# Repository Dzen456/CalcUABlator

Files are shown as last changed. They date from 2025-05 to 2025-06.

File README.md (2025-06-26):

<a href=https://github.com/Dzen456/CalcUABlator>

</a>

<p style="text-align:center;">
A robot capable of doing mathematical operations using Computer Vision.

This document contains instructions of the robot's functionality and usage, and the requirements necessary for this code and hardware to work.
</p>

## Table of contents:

- [Description](#Description)
- [Directories](#Directories)
- [Demo](#Demo)
- [Installation](#Installation)
  - [Hardware](#Hardware)
      - [Fritzing](#Fritzing)
  - [Software](#Software)
      - [Specs](#Specs)
      - [Requirements](#Requirements)
- [Simulation](#Simulation)
- [How to Use](#How_to_Use)
- [Contributions](#Contributions)
- [License](#License)
- [Authors](#Authors)
- [Bibliography](#Bibliography)

## Description:
In this project, we wanted to create a robot capable of solving mathematical operations using Computer Vision and some of the things we learned during this subject. 

On the one hand, when considering this idea, you may think of applications or websites like PhotoMath or Symbolab, so you can think that this robot the same as these apps, but in a more tangible way.

On the other hand, all the pieces used for this robot are recycled: the main structure of the robot is a scara made in 2017, and the camera and Raspberry Pi structure were made from a wooden plank from an old pallet.

Finally, we developed the software to detect an operation, solve it, and write the solution on real paper. We also created a CoppeliaSim scene and a Jupyter Notebook so you can simulate the entire robot process in a simple and visual way.

See <a href=https://github.com/Dzen456/CalcUABlator/blob/main/CREATIVE%20PROCESS.md> CREATIVE PROCESS </a> to read more about the making of this project.

## Directories:

CalcUABlator has the following directories:

- CoppeliaSim_CalcUABlator: This folder contains the CoppeliaSim scene and the Jupyter Notebook of the robot, where you can simulate his behaviour and usage.
```cmd
CoppeliaSim_CalcUABlator/
├── test_texture/
│   └── test_texture.jpg
├── CoppeliaSim.gif
├── CoppeliaSim_CalcUABlator.ttt
├── CoppeliaSim_CalcUABlator_script.ipynb
├── remoteApi.dll
├── sim.py
└── simConst.py
```
- Hardware_CalcUABlator: This folder contains the components, budget and blueprints for the fritzing of the robot, required for his correct construction. The diagram must be followed; otherwise, the robot likely won't work.
```cmd
Hardware_CalcUABlator/
├── Fritzing_CalcUABlator/
│   ├── MSStepperDriverTable.PNG
│   ├── calcUABlator-fritzing.fzz
│   ├── calcUABlator-fritzing_bb.png
│   └── references.txt
├── budget.pdf
├── budget.xlsx
├── components.pdf
└── components.xlsx
```
- Old version - 3D Model and ideas: This folder contains an old, unused version of the robot for researching purposes, with the dimensions, list of components, and a code for the camera.
```cmd
Old version - 3D Model and ideas/
├── OLD_calcUABlator/
│   ├── Pen Holder/
│   │   ├── Comment.txt
│   │   ├── RLP_PenHolder.blend
│   │   ├── part1.png
│   │   ├── part2.png
│   │   ├── part3.png
│   │   └── part4.png
│   ├── background_test/
│   │   └── christmas_photo_studio_07_4k.exr
│   ├── List of components (No Hardware) - 22-04-2025.pdf
│   └── RLP_Robot_sketch2.blend
├── Measurement_Confirmation_Script.py
├── Raspberry_Structure_Measurements.txt
└── Raspberry_Structure_Measurements_Trigonometry (Comments in Spanish).pdf
```
- Software_CalcUABlator: This folder contains the function diagram of the robot, with all the variables and functions that the robot manages in the Raspberry Pi and Arduino modules, all the RaspberryPi and Arduino scripts and a requirements.txt for the installation.
```cmd
Software_CalcUABlator/
├── Arduino/
│   ├── OnlyServo/
│   │   └── sketch_may14a.ino
│   ├── Servo+Steppers/
│   │   └── sketch_may27a.ino
│   └── Main/
│       └── Main.ino
├── RaspberryPi
│   ├── capture_image.py
│   ├── connect_arduino.py
│   ├── main.py
│   ├── move_robot.py
│   └── text_recognition.py
├── SoftwareSchema.pdf
├── requirements.txt
└── specs.txt
```

## Demo:
Click <a href=https://youtu.be/mdDsb5YC6hA> here </a> to see the demo video.
<a href=https://youtu.be/mdDsb5YC6hA>
  


</a>

## Installation:

### Hardware

Making this robot requieres all of the following **hardware components**, or at least similar to:

| <a href=https://tienda.bricogeek.com/arduino-original/1845-arduino-uno-r4-wifi.html> Arduino UNO 4 WiFi </a> | <a href=https://tienda.bricogeek.com/placas-raspberry-pi/1330-raspberry-pi-4-model-b-4-gb.html > Raspberry Pi 4 </a> |
| :---: | :---: |
|  |  |
| <a href=https://tienda.bricogeek.com/accesorios-raspberry-pi/822-camara-raspberry-pi-v2-8-megapixels.html> **Raspberry Pi v2 Cam** </a> | <a href=https://tienda.bricogeek.com/fuentes-de-alimentacion/775-fuente-de-alimentacion-atx-coolbox-500w.html> **Power Supply ATX 500W** </a> |
|  |  |
| <a href=https://tienda.bricogeek.com/motores-paso-a-paso/1360-motor-nema-17-35kg-con-conector-y-cable.html> **Nema 17 stepper** </a> | <a href=https://tienda.bricogeek.com/controladores-motores/553-pololu-a4988-stepstick-prusa-reprap.html> **Stepper Driver Pololu A4988** </a> |
|  |  |
| <a href=https://tienda.bricogeek.com/motores/118-servomotor-de-rotacion-continua-s3003-360-grados.html> **Servo S3003** </a> |  |
|  |  |

<!-- Source Power Supply for Raspberry Pi 4 - 5V/2.5A -->
- You will need to have a **Power Supply for the Raspberry Pi 4 of 5V/2.5A**.
- You should **use the +12V (Yellow output) from the ATX Power Supply** to power the stepper drivers.

- Maybe you should **calibrate the two stepper drivers to a VRef of 1.2V** (see how to do this in this video: https://youtu.be/wcLeXXATCR4?t=462).


#### Fritzing:
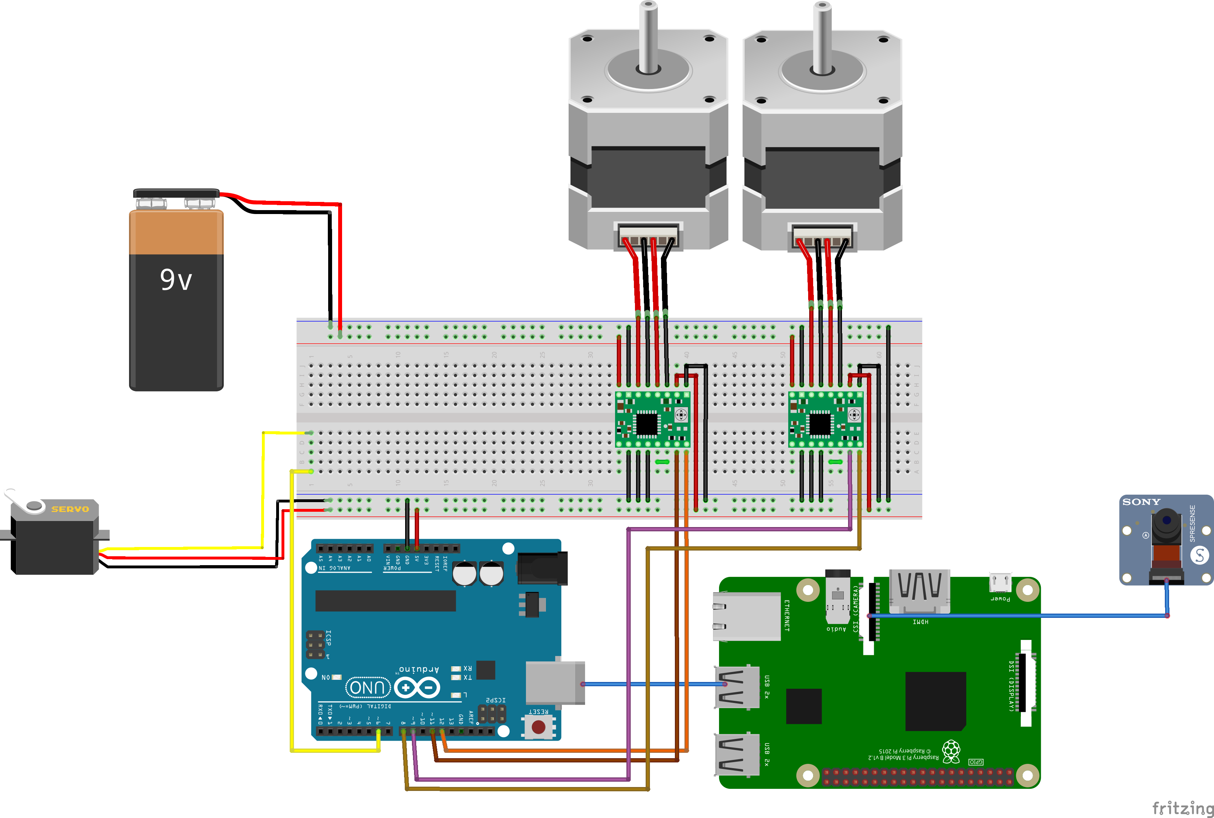
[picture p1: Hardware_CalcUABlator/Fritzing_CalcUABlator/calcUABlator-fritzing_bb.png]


Also, it is required to have the following **additional pieces**:

- Arms Support: (estimated parameters: length - 18 cm / width - 5 cm / thickness - 0.25 cm)
- Big Metal Axis: (estimated parameters: diameter - 2 cm / height - 12 cm)
- Big Axis Wheel: (estimated parameters: wheel diameter - 3 cm / hole wheel diameter - 2 cm)
- Small Metal Axis: (estimated parameters: diameter - 2 cm / height - 5 cm)
- Smal Wheel Axis: (estimated parameters: wheel diameter - 3 cm / hole wheel diameter - 2 cm)
- Screws: 20 screws of 1 cm, 4 screws of 3 cm
- Pen Support Piece: (estimated parameters: length - 5 cm / width - 1 cm / square zone hole - 1x1 cm)
- Wood Platform: (estimated parameters: length - 42 cm / width - 32 cm / thickness - 1 cm)
- Raspberry Structure Support: (estimated parameters: length - 8 cm / width - 8 cm / height - 30 cm)
- Raspberry Structure Superior Support: (estimated parameters: length - 30 cm / width - 8 cm / thickness - 2 cm)
- 2-4 brackets
- Rubber Strap
- Also some extra pieces between the arms and the axis supports.

### Software



#### Specs:

IDEs:
- Python (Pycharm, VS Code, Spyder,...)
- Jupyter Notebook 7+ (Downloaded from the website or Anaconda)
- Arduino IDE (Web or desktop version)

Other software:
- Coppelia 4.7
- Blender 4.1
- Python 3.11

#### Requirements:
```shell
numpy
opencv-python
matplotlib
easyocr
sympy
pyserial
```

If you just want to run the simulation, see [Simulation](#Simulation). 

If you want to make it work in the real life, see [How to Use](#How-to-Use).

## Simulation:

1. Clone this repo.
 ```bash
 git clone https://github.com/Dzen456/CalcUABlator.git
 ```
   
2. You have to open and run the CoppeliaSim_CalcUABlator.ttt file on the CoppeliaSim
3. Then, execute the CoppeliaSim_CalcUABlator_script.ipynb notebook to activate the demo of the robot. It is possible to change the test texture in the folder test_texture to test the robot capacities.
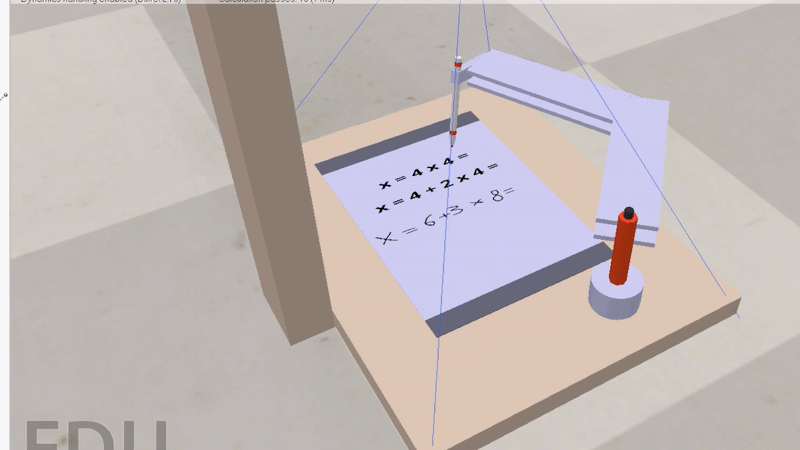
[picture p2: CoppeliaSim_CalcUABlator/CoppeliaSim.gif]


## How to Use:

1. Clone this repo.
 ```bash
 git clone https://github.com/Dzen456/CalcUABlator.git
 ```

2. Install the required libraries.
Using pip:
```bash
pip install requirements.txt
```
Using conda:
```bash
conda install -c requirements.txt
```

3. Execute python script in each directory.

4. To run the robot's Arduino UNO 4 WiFi, you'll have to connect the device to the arduino with a USB cable to be able to run the code correctly. You'll also need to build the robot using the components described [above](#Hardware) and the blueprints for the [circuits](#Fritzing) and structure.

5. Add star to this repo if you like it!

## Contributions:

See <a href=https://github.com/Dzen456/CalcUABlator/blob/main/CONTRIBUTING.md> CONTRIBUTING </a> if you want to contribute to this project.

## License:

This project has a <a href=https://github.com/Dzen456/CalcUABlator/blob/main/LICENSE> Creative Commons License </a>.

## Authors:

- Yanhao Lin
- Isaac Sánchez Amat
- Jofre Segura Montagut
- Raúl Velázquez Gómez
- David Zheng

## Bibliography:

- Arduino UNO R4 Wifi: https://tienda.bricogeek.com/arduino-original/1845-arduino-uno-r4-wifi.html 
- Raspberry Pi 4: https://tienda.bricogeek.com/placas-raspberry-pi/1330-raspberry-pi-4-model-b-4-gb.html 
- Nema 17 stepper: https://tienda.bricogeek.com/motores-paso-a-paso/1360-motor-nema-17-35kg-con-conector-y-cable.html 
- Power Supply ATX 500W: https://tienda.bricogeek.com/fuentes-de-alimentacion/775-fuente-de-alimentacion-atx-coolbox-500w.html 
- Stepper Driver Pololu A4988: https://tienda.bricogeek.com/controladores-motores/553-pololu-a4988-stepstick-prusa-reprap.html 
- Raspberry Pi v2 Cam: https://tienda.bricogeek.com/accesorios-raspberry-pi/822-camara-raspberry-pi-v2-8-megapixels.html 
- Servo S3003: https://tienda.bricogeek.com/motores/118-servomotor-de-rotacion-continua-s3003-360-grados.html

- Getting started with arduino: https://docs.arduino.cc/tutorials/uno-rev3/getting-started/ 
- Connect Raspberry Pi to Arduino: https://www.youtube.com/watch?v=xc9rUI0F6Iw 
- Connect stepper and stepper driver to Arduino (1): https://www.youtube.com/shorts/hTjXpgDDzUI 
- Connect stepper and stepper driver to Arduino (2): 
https://www.youtube.com/watch?v=nLV0fjUWI-g 
- Connect servo motor to Arduino: https://www.youtube.com/watch?v=rM1Zk05Xdlk 
- Connect Raspberry cam to Raspberry Pi: https://www.youtube.com/watch?v=VzYGDq0D1mw 
- Control stepper motor with Arduino: https://docs.arduino.cc/learn/electronics/stepper-motors/ 
- Control servo motor: https://docs.arduino.cc/learn/electronics/servo-motors/ 
- Connect, calibrate and control NEMA 17 steppers with arduino: https://www.youtube.com/watch?v=wcLeXXATCR4 
- Raspberry Pi v2 Cam angles: https://raspberrypi-guide.github.io/electronics/camera-positioning

- Robot from 2017: https://rlpengineeringschooluab2017.wordpress.com/2017/05/30/turing-drawing/
- Robótica, Llenguatge i Programació class notes.

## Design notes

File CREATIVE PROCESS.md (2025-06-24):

# Creative Process

This document explains the creative process of the project.

At first, we discussed a lot of posible ideas for a robot. After long deliberations, we came at the conclusion that it would be interesting to make a robot that would be capable of doing mathematical operations.

This robot may feel useless because there are already other resources that are capable of doing something similar without making a full-sized robot, for example, aplications like PhotoMath or webs like Symbolab, but we thought that it could have some interesting applications at some environments like a school, because it would be easier to teach math using this robot in a more autonomous way, than just writing an operation and making it manually. This, however, required to make a robot capable of doing the process of the operation too, which was inviable due to our time and resources, so we decided to make this robot as a kind of research that could be used at the future for other projects too. Also, these types of online services usually require cookies or other data-collecting methods that would be avoided if a robot is used instead, so it wasn't a bad idea to make something for that purpose.

Our first step was to decide the robot components without surpassing the budget, but we had to order too many things and we had to surpass the budget a bit, but nothing serious. We then started to model the robot: we had to do the base and decide the 3D pieces and the shape of the robot. This was more complex than it sounds, but then we got permission to use another robot as a base for our project, which was very useful and solved a lot of things.

We then started to make the simulation of the robot and we worked on the camera support for the robot as an additional piece. The simulation was made sucessfully and we got wood material from the OpenLabs of our department, material that we modified on these same instalations to obtain the support piece for the camera. We also made the fritzing to knew how the circuits of the robot would be conected for them to work and we also did the functions diagram to have an idea of what would be the programming structure of the robot.

Once we obtained the hardware that we requested, we finally were able to put all of the things together, and make the robot work. But it turned out to not be that easy, because the fritzing didn't work at first. After a long series of trials and errors, we concluded that the problem was one driver that didn't allow the other engine to work fine because we couldn't callibrate it correctly due to his own set limit. We also had to change the principal band because it hadn't enought tension to be able to make the robot work, which was a problem too, and we had to change the drivers a lot of times due to the set limit that didn't allow us to give enough strength to the robot (we knew that the problem was the second driver because we got a driver that worked but we only had one to make all of the robot work). Finally, we could make the robot work after trying a lot of drivers, and we took it home to make the video for the presentation.

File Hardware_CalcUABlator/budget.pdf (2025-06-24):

Name | Price | Units | Total | URL
Arduino UNO Rev. 3 | (€ | 28,98) | 1,00 | (€ | 28,98) https://tienda.bricogeek.com/arduino/305-arduino-uno-r3.html
Raspberry Pi 3 B+ | (€ | 49,97) | 1,00 | (€ | 49,97) https://tienda.bricogeek.com/placas-raspberry-pi/1089-raspberry-pi-3-b-plus.html
Fuente Alimentación Raspberry Pi 3 - 5V/2.5A | (€ | 9,56) | 1,00 | (€ | 9,56) https://tienda.bricogeek.com/accesorios-raspberry-pi/813-alimentador-raspberry-pi-3-5v25a.html
Cámara Raspberry Pi v2 - 8 Megapixels | (€ | 24,14) | 1,00 | (€ | 24,14) https://tienda.bricogeek.com/accesorios-raspberry-pi/822-camara-raspberry-pi-v2-8-megapixels.html
Motor NEMA 17 / 3.5Kg con conector y cable | (€ | 11,13) | 2,00 | (€ | 22,26) https://tienda.bricogeek.com/motores-paso-a-paso/1360-motor-nema-17-35kg-con-conector-y-cable.html
Controlador de motores paso a paso 3.5A (TB6600) | (€ | 24,14) | 2,00 | (€ | 48,28) https://tienda.bricogeek.com/controladores-motores/992-controlador-de-motores-paso-a-paso-35a-tb6600.html
Servo estándar S3003, 360 Grados | (€ | 6,66) | 1,00 | (€ | 6,66) https://tienda.bricogeek.com/motores/118-servomotor-de-rotacion-continua-s3003-360-grados.html
(Piezas de soporte para los controladores?)
Fuente de alimentación ATX COOLBOX 500W | 19,97 | 1 | 19,97 https://tienda.bricogeek.com/fuentes-de-alimentacion/775-fuente-de-alimentacion-atx-coolbox-500w.html
TOTAL | (€ 209,82)
*Suposem que es pot alimentar l'arduino amb la ATX*
(Si no, faria falta una alimentació per l'arduino)

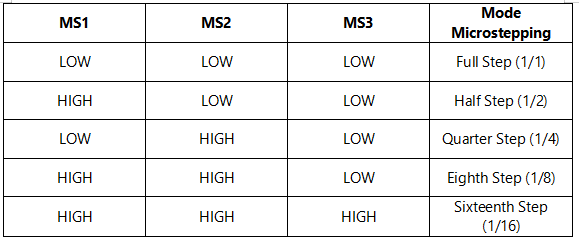
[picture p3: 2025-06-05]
Hardware_CalcUABlator/Fritzing_CalcUABlator/MSStepperDriverTable.PNG

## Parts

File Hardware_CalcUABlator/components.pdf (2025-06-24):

| Largo (mm) | Ancho (mm) | Alto (mm) | Peso (g) | Plano medidas | Plano conexiones | Datos/contenido adcional
Arduino UNO R3 | 68.6 | 53.2 | 12.5 | 25 | Ver Medidas (https://kicad-info.s3.dualstack.us-west-2.amazonaws.com/original/2X/e/ed545e8aaf2ff57f95a87286ba8bb29ea2749de6.jpeg) | Ver circuito (https://www.jameco.com/Jameco/workshop/CircuitNotes/arduino-uno-pinout.png)
Raspberry Pi 3 B+ (https://tienda.bricogeek.com/placas-raspberry-pi/1089-raspberry-pi-3-b-plus.html) | 85.0 | 56.0 | 17.0 | 60 | Ver Medidas (https://raspiworld.com/images/other/drawings/Raspberry-Pi-1-2-3-Model-B.jpg) | Ver circuito (https://www.jameco.com/Jameco/workshop/CircuitNotes/raspberry_pi_circuit_note_fig2.jpg) | Vídeo de como connectar raspberry a arduino (https://www.youtube.com/watch?v=xc9rUI0F6Iw)
Fuente Alimentación Raspberry Pi 3 - 5V/2.5A (https://tienda.bricogeek.com/accesorios-raspberry-pi/813-alimentador-raspberry-pi-3-5v25a.html) | 73.2 | 45.1 | 35.1 | 150
Cámara Raspberry Pi v2 - 8 Megapixels (https://tienda.bricogeek.com/accesorios-raspberry-pi/822-camara-raspberry-pi-v2-8-megapixels.html) | 25.0 | 24.0 | 9.0 | 3 | Ver Medidas (https://www.raspberrypi-spy.co.uk/wp-content/uploads/2013/05/Raspberry-Pi-Camera-Module-Diagram.png) | Ver circuito (https://docs.arducam.com/Raspberry-Pi-Camera/Low-Light/picture/arducam_wiki_rpi_imx708_hardware_picture_1.png) | Campo de visión horizontal (CdV): 62,2 grados. Campo de visión vertical (CdV): 48,8 grados, Vídeo de como connectar la camara raspberry pi
Motor NEMA 17 / 3.5Kg con conector y cable x2 (https://tienda.bricogeek.com/motores-paso-a-paso/1360-motor-nema-17-35kg-con-conector-y-cable.html) | 42.0 | 42.0 | 40.0 | 270 | Ver Medidas (https://tienda.bricogeek.com/1820-thickbox_default/motor-paso-a-paso-nema-17-32kg-cm.jpg) | Ver circuito (https://protosupplies.com/wp-content/uploads/2018/04/DRV8825-Driver-Minimal-Setup.jpg) | Vídeo de como conectar controlador de motores y steppers con arduino , Otro vídeo
Controlador de motores paso a paso 3.5A (TB6600) x2 (https://tienda.bricogeek.com/controladores-motores/992-controlador-de-motores-paso-a-paso-35a-tb6600.html) | 96.0 | 56.0 | 33.0 | 200 | Ver Medidas (https://comtongkorea.cafe24.com/web/image/2218_KC0001024/640602054294/D640602054294_9.jpg) | Ver circuito (https://tienda.bricogeek.com/4135-large_default/controlador-de-motores-paso-a-paso-35a-tb6600.jpg) | Vídeo de como conectar controlador de motores y steppers con arduino (https://www.youtube.com/shorts/hTjXpgDDzUI)
Servo estándar S3003, 360 Grados (https://tienda.bricogeek.com/motores/118-servomotor-de-rotacion-continua-s3003-360-grados.html) | 39.5 | 20.0 | 35.6 | 53 | Ver Medidas (https://tienda.bricogeek.com/9440-thickbox_default/servo-6-kg-300-grados-con-proteccion.jpg) | Ver circuito (https://cdn.shopify.com/s/files/1/0587/2130/4757/files/KG085.jpg?v=1638961040) | Vídeo de como conectar servo motor al arduino (https://www.youtube.com/watch?v=rM1Zk05Xdlk)
Fuente de alimentación ATX COOLBOX 500W (https://tienda.bricogeek.com/fuentes-de-alimentacion/775-fuente-de-alimentacion-atx-coolbox-500w.html) | 140.0 | 150.0 | 85.0 | 2180

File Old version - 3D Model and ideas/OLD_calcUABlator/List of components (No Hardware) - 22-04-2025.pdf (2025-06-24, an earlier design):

Arm supports: To be determined.
- Estimate:
- Length: 18 cm
- Width: 5 cm
- Thickness: 0.25 cm

Intermediate pieces between arms and axle supports: To be determined.

Large axle (Metal):
- Diameter: 2 cm
- Height: About 12 cm

Large axle wheel (3D printed):
- Wheel diameter: 3 cm
- Hole diameter: 2 cm (goes to the large axle)

Small axle (Metal):
- Diameter: 2 cm
- Height: About 5 cm

Small axle wheel (3D printed):
- Wheel diameter: 3 cm
- Hole diameter: 2 cm (goes to the small axle)

Screws (Estimate):
- About 20 units,1 cm long
- About 4 bigger, about 3 cm long (Those that go into the wood, in the Raspberry structure, above)

Pen holder piece (3D printed):
- Length: 5 cm
- Width: 1 cm
- Square hole area, approximately 1x1 cm

Wooden platform:
- Length: 42 cm
- Width: 32 cm
- Thickness: 1 cm

DC bracket, Arm 1, to be determined

Raspberry structure:
- Base support (still to be determined with camera angles, wood):
- Length: 8 cm
- Width: 8 cm
- Height: 30 cm
- Upper support (where the camera goes, wood):
- Length: 30 cm
- Width: 8 cm
- Thickness: 2 cm

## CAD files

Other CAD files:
Old version - 3D Model and ideas/OLD_calcUABlator/Pen Holder/RLP_PenHolder.blend
Old version - 3D Model and ideas/OLD_calcUABlator/RLP_Robot_sketch2.blend

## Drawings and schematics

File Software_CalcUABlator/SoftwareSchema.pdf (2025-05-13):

# SOFTWARE SCHEMA

# Raspberry Pi

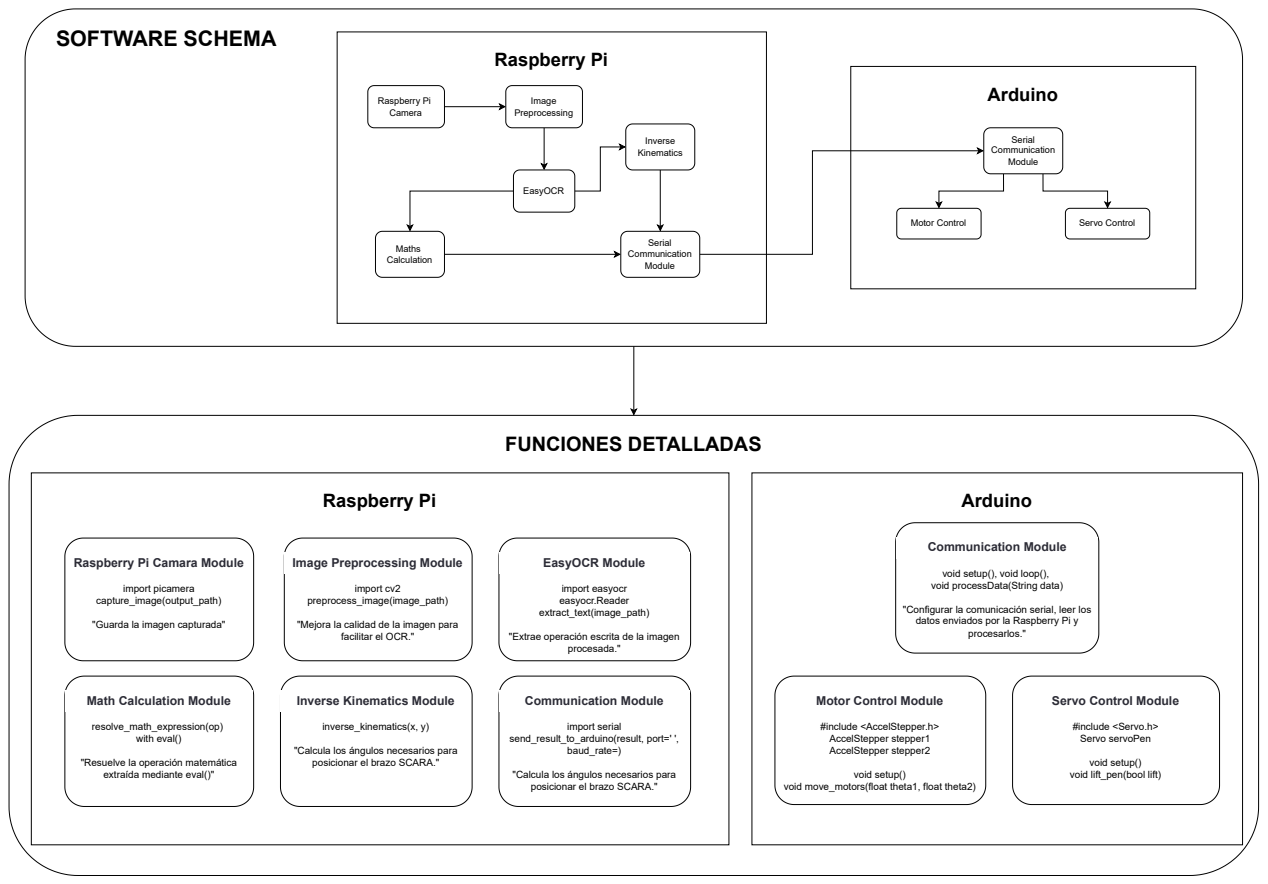
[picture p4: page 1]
Raspberry Pi; Arduino; Camera; Image Preprocessing; EasyOCR; Maths Calculation; Inverse Kinematics; Serial Communication Module; Motor Control; Servo Control; import picamera capture_image(output_path); import cv2 preprocess_image(image_path); EasyOCR Module; import easyocr easyocr.Reader extract_text(image_path); procesada."; resolve_math_expression(op) with eval(); inverse_kinematics(x, y); Communication Module; import serial send_result_to_arduino(result, port=' ', baud_rate=)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

Raspberry Pi Camara Module

Image Preprocessing Module

void setup(), void loop(),
void processData(String data)

"Configurar la comunicación serial, leer los
datos enviados por la Raspberry Pi y

"Guarda la imagen capturada"

"Mejora la calidad de la imagen para

facilitar el OCR."

"Extrae operación escrita de la imagen

Math Calculation Module

Inverse Kinematics Module

Motor Control Module

Servo Control Module

"Calcula los ángulos necesarios para
posicionar el brazo SCARA."

"Resuelve la operación matemática
extraída mediante eval()"

void setup()
void lift_pen(bool lift)

void move_motors(float theta1, float theta2)

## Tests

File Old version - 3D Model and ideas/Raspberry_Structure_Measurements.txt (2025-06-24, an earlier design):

Ideal Woods:

Regarding height:
One 40.5 cm, which will be the support, and then the top piece, which will be 2 cm high.

Base square:
8x8? cm

Top piece rectangle:
8? x 20+8? -> Depends on the previous piece.

Final Measurements (If possible):

Base piece:

Height: 40.5 cm
Width: 8 cm
Length: 8 cm

Top piece (where the camera will go):

Height: 2 cm
Width: 8 cm
Length: 28 cm

We'll see what we can get at the Open Labs.

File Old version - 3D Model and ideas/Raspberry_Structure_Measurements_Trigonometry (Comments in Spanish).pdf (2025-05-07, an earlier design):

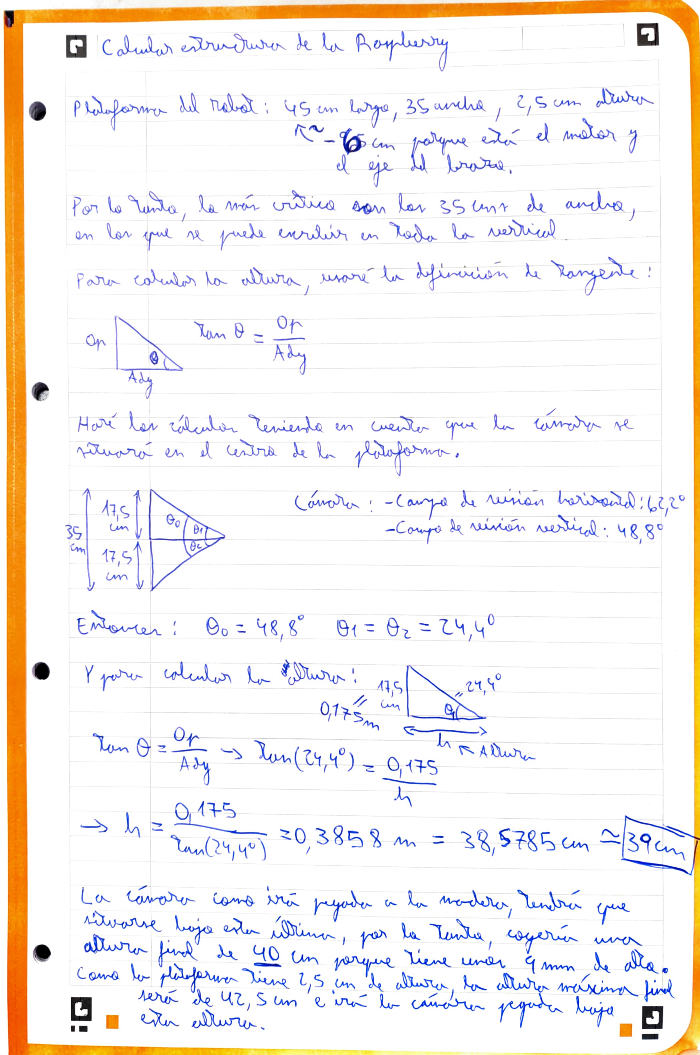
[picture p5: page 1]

Eeen

Bo

Aby
75

tgo,3swndha

0175m
Lon(r,) 915

z0 38 m = 38,5785 Cn 39

wn

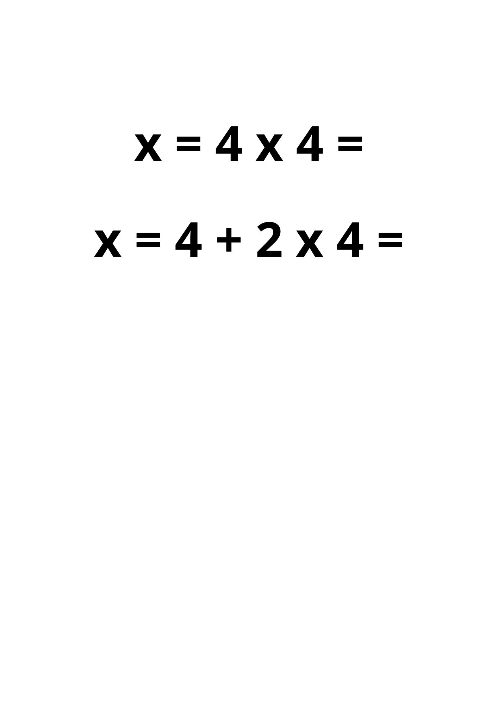
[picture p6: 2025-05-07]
CoppeliaSim_CalcUABlator/test_texture/test_texture.jpg

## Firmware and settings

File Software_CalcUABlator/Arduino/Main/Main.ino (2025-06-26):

#include <AccelStepper.h>
#include <Servo.h>

// Configuración del pin del servomotor
#define SERVO_PIN 6

// Crear un objeto Servo
Servo penServo;

// Configuración de los pines para los motores
#define MOTOR1_PIN_STEP 11
#define MOTOR1_PIN_DIR 12
#define MOTOR2_PIN_STEP 9
#define MOTOR2_PIN_DIR 8

const int width = 50, height = 50; // Ancho y alto del dígito

// Ángulo de rotación (en grados)
const float rotation_angle_degrees = -20.0; // Ajusta este valor según sea necesario
const float rotation_angle_radians = rotation_angle_degrees * PI / 180.0;

// Crear objetos AccelStepper para cada motor
AccelStepper stepper1(AccelStepper::DRIVER, MOTOR1_PIN_STEP, MOTOR1_PIN_DIR);
AccelStepper stepper2(AccelStepper::DRIVER, MOTOR2_PIN_STEP, MOTOR2_PIN_DIR);

bool stopRunning = false;
void setup() {
  Serial.begin(9600);  // Inicializar comunicación serial
  
  // Configurar velocidad máxima y aceleración para cada motor
  stepper1.setMaxSpeed(1000);
  stepper1.setAcceleration(500);
  
  stepper2.setMaxSpeed(1000);
  stepper2.setAcceleration(500);

  // Adjuntar el servomotor al pin especificado
  penServo.attach(SERVO_PIN);

  // Posición inicial (bolígrafo levantado)
  lift_pen(true);
}

void move_to_position_rotated(int x, int y, int centerX, int centerY) {
  int* rotatedCoords = rotate_point(x, y, centerX, centerY);
  int rotatedX = rotatedCoords[0];
  int rotatedY = rotatedCoords[1];

  // Mover los motores a las coordenadas rotadas
  stepper1.moveTo(rotatedX);
  stepper2.moveTo(rotatedY);

  while (stepper1.distanceToGo() != 0 || stepper2.distanceToGo() != 0) {
    stepper1.run();
    stepper2.run();
  }
}

int* rotate_point(int x, int y, int centerX, int centerY) {
  // Calcular las coordenadas relativas al centro
  int relativeX = x - centerX;
  int relativeY = y - centerY;

  // Aplicar la fórmula de rotación
  float rotatedX = relativeX * cos(rotation_angle_radians) - relativeY * sin(rotation_angle_radians);
  float rotatedY = relativeX * sin(rotation_angle_radians) + relativeY * cos(rotation_angle_radians);

  // Volver a la posición absoluta
  static int rotatedCoords[2];
  rotatedCoords[0] = round(rotatedX + centerX);
  rotatedCoords[1] = round(rotatedY + centerY);
  return rotatedCoords;
}

void write_number(int number) {
  // Levantar el bolígrafo antes de empezar
  lift_pen(true);

  // Obtener la posición actual del brazo
  int currentX = stepper1.currentPosition();
  int currentY = stepper2.currentPosition();

  // Mover al punto inicial relativo a la posición actual

  // Dibujar el número según el valor recibido
  switch (number) {
    case 0:
      draw_zero(currentX, currentY);
      break;
    case 1:
      draw_one(currentX, currentY);
      break;
    case 2:
      draw_two(currentX, currentY);
      break;
    case 3:
      draw_three(currentX, currentY);
      break;
    case 4:
      draw_four(currentX, currentY);
      break;
    case 5:
      draw_five(currentX, currentY);
      break;
    case 6:
      draw_six(currentX, currentY);
      break;
    case 7:
      draw_seven(currentX, currentY);
      break;
    case 8:
      draw_eight(currentX, currentY);
      break;
    case 9:
      draw_nine(currentX, currentY);
      break;
    default:
      Serial.println("Número no válido.");
      return;
  }

  // Levantar el bolígrafo después de terminar
  lift_pen(true);
}

void loop() {
  if (stopRunning == true) {
    return;
  }
  if (Serial.available() > 0) {
    String receivedData = Serial.readStringUntil('\n');  // Read until newline character
    receivedData.trim();  // Remove any extra whitespace or carriage returns

    // Split the string into three parts using the delimiter (comma)
    int firstCommaIndex = receivedData.indexOf(',');
    int secondCommaIndex = receivedData.indexOf(',', firstCommaIndex + 1);

    if (firstCommaIndex != -1 && secondCommaIndex != -1) {  // Ensure delimiters exist
      String value1Str = receivedData.substring(0, firstCommaIndex);
      String value2Str = receivedData.substring(firstCommaIndex + 1, secondCommaIndex);
      String value3Str = receivedData.substring(secondCommaIndex + 1);

      // Convertir a int
      int value1 = value1Str.toInt();
      int value2 = value2Str.toInt();
      int value3 = value3Str.toInt();

      Serial.print("Received Value 1: ");
      Serial.println(value1);
      Serial.print("Received Value 2: ");
      Serial.println(value2);
      Serial.print("Received Value 3: ");
      Serial.println(value3);
      
      stepper1.moveTo(value1 * (200.0 / 360.0) + 40);  // Convierte grados a pasos
      while (stepper1.distanceToGo() != 0) {
        stepper1.run(); 
      }
      delay(1000);  // Esperar 1 segundo

      stepper2.moveTo(value2 * (200.0 / 360.0) - 100);  // Convierte grados a pasos
      while (stepper2.distanceToGo() != 0) {
        stepper2.run();
      }
      delay(1000);

      write_number(value3);
      stopRunning = true;
      return;
      
    }
  }
  /*
  lift_pen(false);
  delay(1000);
  lift_pen(true);
  delay(1000);
  */
}

void draw_zero(int startX, int startY) {
  lift_pen(false);  // Bajar el bolígrafo
  move_to_position_rotated(startX, startY, startX, startY);                  // Punto inicial
  move_to_position_rotated(startX + width, startY, startX, startY);          // Línea horizontal superior
  move_to_position_rotated(startX + width, startY + height, startX, startY); // Línea vertical derecha
  move_to_position_rotated(startX, startY + height, startX, startY);         // Línea horizontal inferior
  move_to_position_rotated(startX, startY, startX, startY);                  // Línea vertical izquierda
  lift_pen(true);  // Levantar el bolígrafo
}

void draw_one(int startX, int startY) {
  lift_pen(false);  // Bajar el bolígrafo
  move_to_position_rotated(startX + width / 2, startY, startX, startY);       // Punto inicial
  move_to_position_rotated(startX + width / 2, startY + height, startX, startY); // Línea vertical
  lift_pen(true);  // Levantar el bolígrafo
}

void draw_two(int startX, int startY) {
  lift_pen(false);  // Bajar el bolígrafo
  move_to_position_rotated(startX, startY, startX, startY);                   // Punto inicial
  move_to_position_rotated(startX + width, startY, startX, startY);           // Línea horizontal superior
  move_to_position_rotated(startX + width, startY + height / 2, startX, startY); // Línea diagonal derecha
  move_to_position_rotated(startX, startY + height / 2, startX, startY);      // Línea horizontal central
  move_to_position_rotated(startX, startY + height, startX, startY);          // Línea vertical izquierda
  move_to_position_rotated(startX + width, startY + height, startX, startY);  // Línea horizontal inferior
  lift_pen(true);  // Levantar el bolígrafo
}

void draw_three(int startX, int startY) {
  lift_pen(false);  // Bajar el bolígrafo
  move_to_position_rotated(startX, startY, startX, startY);                   // Punto inicial
  move_to_position_rotated(startX + width, startY, startX, startY);           // Línea horizontal superior
  move_to_position_rotated(startX + width, startY + height / 2, startX, startY); // Línea vertical derecha
  move_to_position_rotated(startX, startY + height / 2, startX, startY);      // Línea horizontal central
  move_to_position_rotated(startX + width, startY + height / 2, startX, startY); // Línea vertical derecha
  move_to_position_rotated(startX + width, startY + height, startX, startY);  // Línea horizontal inferior
  lift_pen(true);  // Levantar el bolígrafo
}

void draw_four(int startX, int startY) {
  lift_pen(false);  // Bajar el bolígrafo
  move_to_position_rotated(startX, startY, startX, startY);                   // Punto inicial
  move_to_position_rotated(startX, startY + height / 2, startX, startY);      // Línea vertical izquierda
  move_to_position_rotated(startX + width, startY + height / 2, startX, startY); // Línea horizontal central
  move_to_position_rotated(startX + width, startY, startX, startY);           // Línea vertical derecha
  move_to_position_rotated(startX + width, startY + height, startX, startY);  // Línea vertical derecha
  lift_pen(true);  // Levantar el bolígrafo
}

void draw_five(int startX, int startY) {
  lift_pen(false);  // Bajar el bolígrafo
  move_to_position_rotated(startX + width, startY, startX, startY);           // Punto inicial
  move_to_position_rotated(startX, startY, startX, startY);                   // Línea horizontal superior
  move_to_position_rotated(startX, startY + height / 2, startX, startY);      // Línea vertical izquierda
  move_to_position_rotated(startX + width, startY + height / 2, startX, startY); // Línea horizontal central
  move_to_position_rotated(startX + width, startY + height, startX, startY);  // Línea vertical derecha
  move_to_position_rotated(startX, startY + height, startX, startY);          // Línea horizontal inferior
  lift_pen(true);  // Levantar el bolígrafo
}

void draw_six(int startX, int startY) {
  lift_pen(false);  // Bajar el bolígrafo
  move_to_position_rotated(startX + width, startY, startX, startY);           // Punto inicial
  move_to_position_rotated(startX, startY, startX, startY);                   // Línea horizontal superior
  move_to_position_rotated(startX, startY + height, startX, startY);          // Línea vertical izquierda
  move_to_position_rotated(startX + width, startY + height, startX, startY);  // Línea horizontal inferior
  move_to_position_rotated(startX + width, startY + height / 2, startX, startY); // Línea vertical derecha
  move_to_position_rotated(startX, startY + height / 2, startX, startY);      // Línea horizontal central
  lift_pen(true);  // Levantar el bolígrafo
}

void draw_seven(int startX, int startY) {
  lift_pen(false);  // Bajar el bolígrafo
  move_to_position_rotated(startX, startY, startX, startY);                   // Punto inicial
  move_to_position_rotated(startX + width, startY, startX, startY);           // Línea horizontal superior
  move_to_position_rotated(startX + width / 2, startY + height, startX, startY); // Línea diagonal
  lift_pen(true);  // Levantar el bolígrafo
}

void draw_eight(int startX, int startY) {
  lift_pen(false);  // Bajar el bolígrafo
  move_to_position_rotated(startX, startY, startX, startY);                   // Punto inicial
  move_to_position_rotated(startX + width, startY, startX, startY);           // Línea horizontal superior
  move_to_position_rotated(startX + width, startY + height, startX, startY);  // Línea vertical derecha
  move_to_position_rotated(startX, startY + height, startX, startY);          // Línea horizontal inferior
  move_to_position_rotated(startX, startY, startX, startY);                   // Línea vertical izquierda
  move_to_position_rotated(startX + width, startY + height / 2, startX, startY); // Línea horizontal central
  lift_pen(true);  // Levantar el bolígrafo
}

void draw_nine(int startX, int startY) {
  lift_pen(false);  // Bajar el bolígrafo
  move_to_position_rotated(startX + width, startY + height / 2, startX, startY); // Punto inicial
  move_to_position_rotated(startX, startY + height / 2, startX, startY);      // Línea horizontal central
  move_to_position_rotated(startX, startY, startX, startY);                   // Línea vertical izquierda
  move_to_position_rotated(startX + width, startY, startX, startY);           // Línea horizontal superior
  move_to_position_rotated(startX + width, startY + height, startX, startY);  // Línea vertical derecha
  lift_pen(true);  // Levantar el bolígrafo
}


void lift_pen(bool lift) {
  if (lift) {
    penServo.write(40);  // Ángulo para levantar el bolígrafo
    Serial.println("Bolígrafo levantado.");
  } else {
    penServo.write(-10);   // Ángulo para bajar el bolígrafo
    Serial.println("Bolígrafo bajado.");
  }
}

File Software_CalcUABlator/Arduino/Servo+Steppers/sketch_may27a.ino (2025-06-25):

#include <Servo.h>

// Script that moves the two nema 17 steppers and the servo motor

const int dirPin1 = 12;
const int stepPin1 = 11;

const int dirPin2 = 8;
const int stepPin2 = 9;

Servo myservo;  // create servo object to control a servo
// twelve servo objects can be created on most boards

int pos = 0;    // variable to store the servo position
int d = 0;

void setup() {
  myservo.attach(6);  // attaches the servo on pin 9 to the servo object

  // put your setup code here, to run once:
  pinMode(dirPin1, OUTPUT);
  pinMode(stepPin1, OUTPUT);
  pinMode(dirPin2, OUTPUT);
  pinMode(stepPin2, OUTPUT);
  delay(2000);
  digitalWrite(dirPin1, LOW);
  digitalWrite(dirPin2, LOW);
}

void loop() {
  myservo.write(pos);
  if (d > 60){
    if (pos == 0)
      pos = 30;
    else if (pos == 30)
      pos = 0;
    d = 0;
  }

  // put your main code here, to run repeatedly:
  digitalWrite(stepPin1, HIGH);
  digitalWrite(stepPin2, HIGH);
  delay(25);
  digitalWrite(stepPin1, LOW);
  digitalWrite(stepPin2, LOW);
  delay(25);
  d = d + 1;
}

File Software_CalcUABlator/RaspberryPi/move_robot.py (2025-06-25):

from sympy.physics.mechanics import dynamicsymbols
from sympy import *
import numpy as np

PIXELS_PAPERX=780
PIXELS_PAPERY=1135

CM_PAPERX=21
CM_PAPERY=29.7
scale_factor_x= PIXELS_PAPERX/CM_PAPERX
scale_factor_y = PIXELS_PAPERY/CM_PAPERY

theta1, theta2 = dynamicsymbols('theta1 theta2')

def transform_coordinates(image_coordinates):
	y_robot = image_coordinates[0] / scale_factor_x #- 19
	x_robot = image_coordinates[1] /scale_factor_y #+ 28
	return x_robot, y_robot
	
def calculate_angles(x, y):
	L1=20
	L2=20
	eq1 = (L1 * cos(theta1) + L2 * cos(theta1 + theta2)) - x
	eq2 = (L1 * sin(theta1) + L2 * sin(theta1 + theta2)) - y

	try:
		q = nsolve((eq1, eq2), (theta1, theta2), (1,1), prec=5)
	  
	except Exception as e:
		print("Error:", str(e))
		q = [0, 0, 0, 0]

	q[0] = q[0] - round(q[0] / (np.pi * 2)) * 2 * np.pi
	q[1] = q[1] - round(q[1] / (np.pi * 2)) * 2 * np.pi

	q[0] = round(q[0] * 180 / np.pi,2)
	q[1] = round(q[1] * 180 / np.pi,2)

	return q

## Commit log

2025-04-20 Haciendo el boceto del modelo final y refinando tamaños
    [RLP_Robot_Boceto2.blend]
2025-04-21 Modificaciones y actualizaciones en el sistema del segundo brazo y cambiada la pieza que aguantaría el bolígrafo
    [RLP_Robot_Boceto2.blend]
2025-04-22 Primera versión del Fritzing
    [calcUABlator-fritzing.fzz]
2025-04-22 Lista de Piezas del Robot
2025-04-29 Medidas Estructura Raspberry con cálculos
    [RLP_Robot_Boceto2.blend]
2025-04-29 Add camara y conexiones motor drivers
    [calcUABlator-fritzing.fzz]
2025-05-02 Añadida la estructura del Raspberry, la cámara y demo script obteniendo las imágenes del sensor y las ecuaciones
2025-05-07 Add Fritzing folder
    [calcUABlator-fritzing.fzz]
2025-05-07 Preparing to merge to main
    [RLP_Robot_Boceto2.blend]
2025-05-11 Añadido reconocimiento de expresiones matemáticas al Coppelia
2025-05-13 Añadido conversión de coordenadas entre imagen y escena al Coppelia
    Falta aplicar cinemática inversa para obtener los ángulos de los motores y escribir el resultado
2025-05-14 Añadido Escritura de resultado al Coppelia
2025-05-25 Update Fritzing
    [calcUABlator-fritzing.fzz]
2025-06-05 hotfix Fritzing
    [calcUABlator-fritzing.fzz]
2025-06-24 English translation
    [RLP_Robot_Boceto2.blend, RLP_Robot_sketch2.blend]
2025-06-24 Adding Pen Holder Initial Idea
    [RLP_PenHolder.blend]
2025-06-24 Adding Hardware folder
    [budget.xlsx, calcUABlator-fritzing.fzz, components.xlsx]
2025-06-25 Adding arduino scripts
2025-06-25 Adding Raspberry Files
2025-06-26 Added Arduino main script
